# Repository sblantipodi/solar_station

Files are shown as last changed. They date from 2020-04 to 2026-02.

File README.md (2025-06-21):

# Solar Station
Smart solar watering system  
_Written for Arduino IDE and PlatformIO._







If you like **Solar Station**, give it a star, or fork it and contribute!




Project is bootstrapped with my [Arduino Bootstrapper](https://github.com/sblantipodi/arduino_bootstrapper) library and my [PlatformIO version increment](https://github.com/sblantipodi/platformio_version_increment) script.

## Credits
- Davide Perini

## Components:
  - Arduino C++ sketch running on an ESP8266EX D1 Mini from Lolin running at 80MHz or ESP32-S3
  - Raspberry + Home Assistant for Web GUI, automations and MQTT server
  - 88x142 5V solar panel
  - Sony VCT6 18650 Lithium Battery
  - TP4056 protected lithium charger
  - MT3608 DC DC step up module to step up battery voltage @ 5.5V, ESP chip is happy with it
  - MT3608 DC DC step up module to step up battery voltage @ 8.66V, water pump is powerful with it
  - Relay Shield to safely power the water pump and "detach it from the circuit"
  - (100kΩ + (22kΩ + 4.7kΩ)) voltage divider for Battery voltage level monitoring circuit (see Voltage divider section for ESP32-S3)
  - 3.5V/9V water pump (3W @ 9V)
  - TTP223 capacitive touch button with A contact soldered (HIGH signal when button is not pressed, 
    LOW signal when button is pressed), used to reset the microcontroller
  - Google Home Mini for Voice Recognition
  
## Schematic  
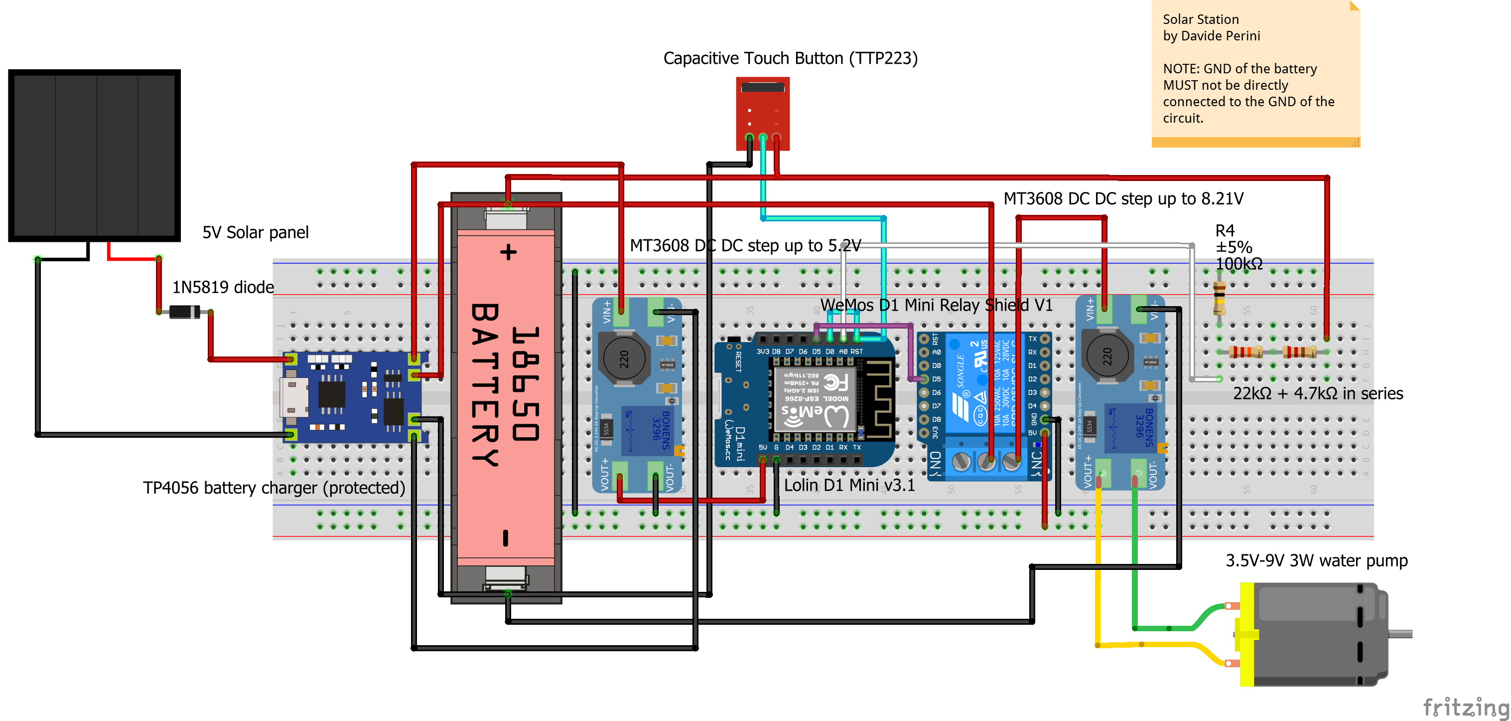
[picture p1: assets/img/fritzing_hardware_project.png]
CIRCUITS


## First working project


## Final working project with two DC to DC step up modules
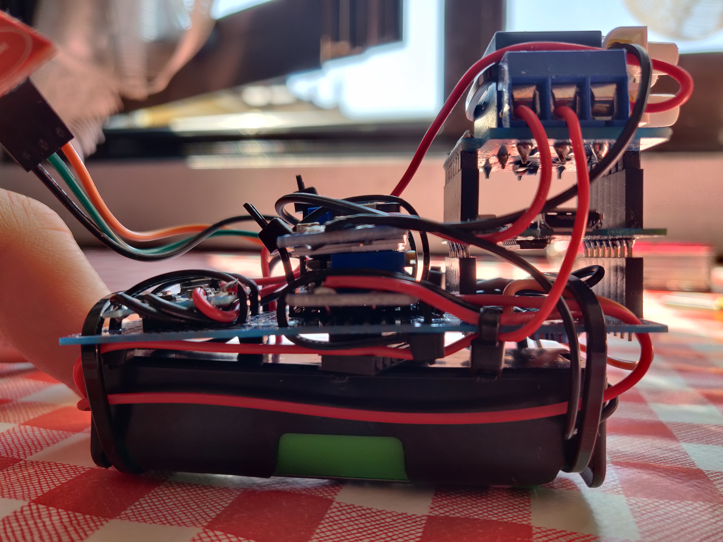
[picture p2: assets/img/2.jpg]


## Voltage divider:

- Voltage source = 4.2V (lithium battery at max)
- R1 = 100kΩ 
- R2 = 22kΩ + 4.7kΩ (in series)
- Voltage Out = 3.3V (maximum voltage that a D1 Mini can read from the analog pin)

EDIT: Project has been updated to work with an ESP32-S3. ESP32-S3 ADC pin reads up to 3.1V (with an attenuation of 11DB),
for this reason I swapped the R2 resistors with a 22kΩ + 10kΩ + 4.7kΩ (in series).

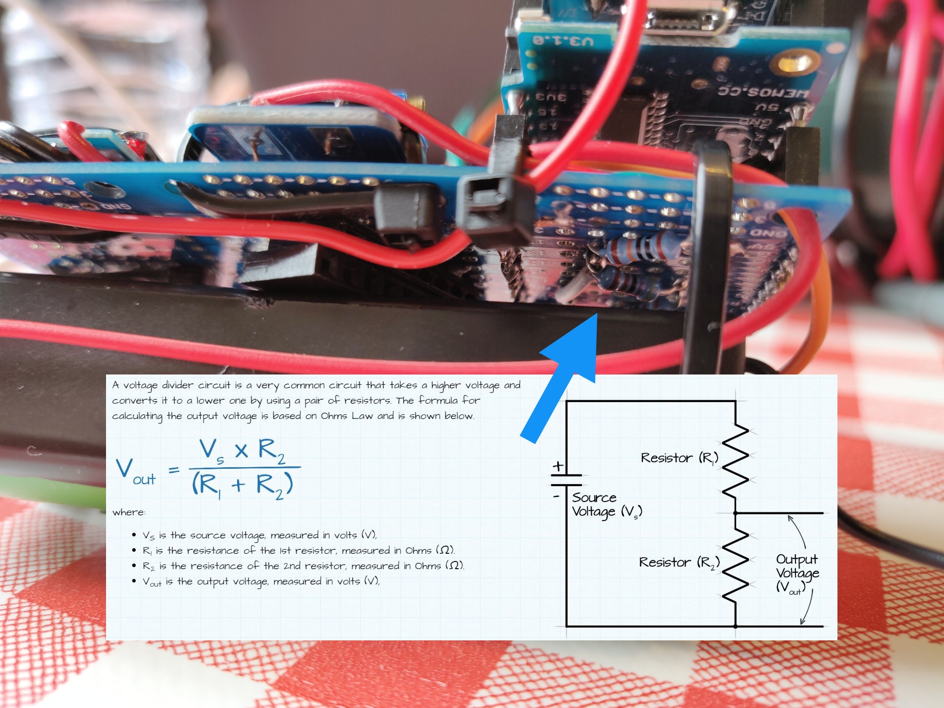
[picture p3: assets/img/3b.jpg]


## From the top
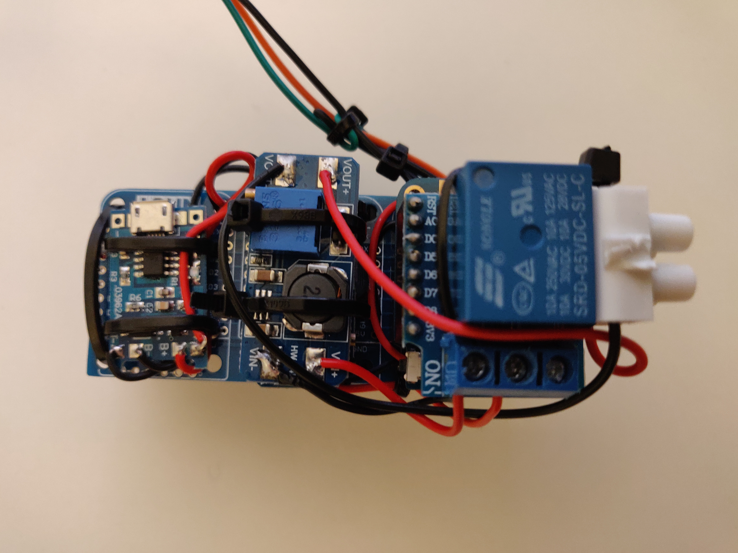
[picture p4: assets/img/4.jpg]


## Water pump
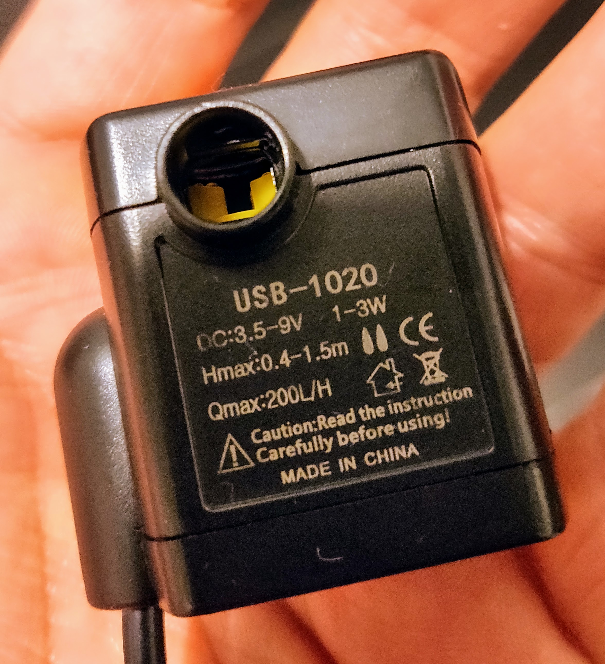
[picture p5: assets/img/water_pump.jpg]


## IP56 box


## Second iteration of the same project for other plants in a non stacked format
  

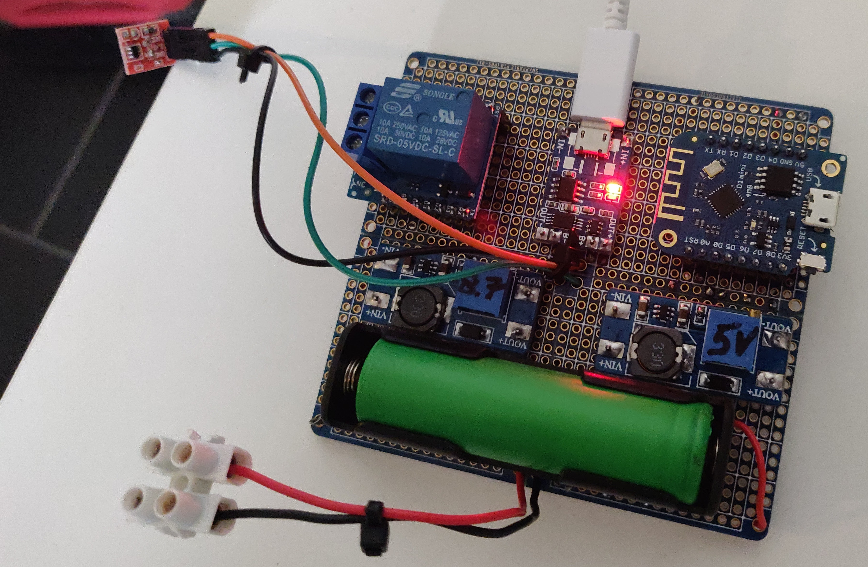
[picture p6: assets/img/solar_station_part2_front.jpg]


## Home Assistant Mobile Client Screenshots
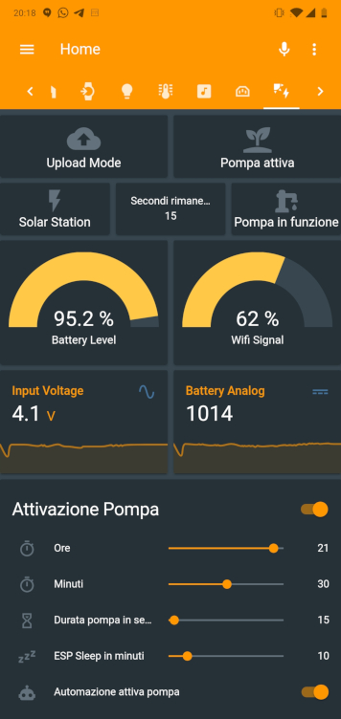
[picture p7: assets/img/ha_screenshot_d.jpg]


## License
This program is licensed under MIT License

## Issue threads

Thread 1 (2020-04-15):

Questions

bobkelso974, 2020-04-15:
Hello
I'm interested in your project
I'd like to ask you a few questions:
What model of water pump do you use?
How long do you run this pump? (deep sleep time?)
Is it for indoor or outdoor use?
And finally, does it work well?

I made about the same circuit.
Except I didn't put a relay but a Mosfet for energy saving.

Thank you

sblantipodi, 2020-04-26:
@bobkelso974 sorry for the late reply.
I'm using a 3.5V-9V 1-3W water pump.

I have added an image of the pump in the readme of the project.
https://github.com/sblantipodi/solar_station

You can find similar pump on amazon, it works very very well.
I run it at 8.6V so a little bit less than 3W and it is very powerful and quiet.

Pump runs for 30 seconds a day because I use it for a small watering system.
Take a look at the readme, there is an IP56 box for outdoor use.
The ESP sleeps for 10 minutes and it stays on the time needed to read the configuration from the MQTT server and send back its state.
Basically when the ESP wake up reads the configuration from the MQTT server, this config says to the ESP if the pump must be on and the number of seconds that it must be turned on.

I can say that the system works very very well.

bobkelso974, 2020-04-27:
Thank you for your answers.
I have the same model of water pump as you but I have a problem, I have almost the same circuit as you expected the relay is replaced by a mosfet
The problem is on my mt3608. When I set the voltage to 8v, I have a hiss on this module and when the pump is running the voltage goes up to 10v ...
When I test with a mini USB boost converter 3V-5V, it works well. I tested several MT3608 same problem
Did you have the same type of problem? Or do you have an idea where it can come from?

sblantipodi, 2020-04-27:
mmm...
A hiss is not necessary a problem, it could be the normal "coil whine" but it's not normal that if you set the MT3608 to output 8V it output 10V.

Is your MT3608 connected to the battery directly like in my circuit?
If your battery able to handle the load of the pump?
Battery tends to have a big voltage drop when something like a motor is connected, after the motor startup the voltage returns to normal and this may cause some spikes.
A good capacitor can help with this problem or probably try to choose a better 18650 battery rated for high drain. I know that 3W is not that much for a 18650 (I hope you are using a 18650) but motors are a bit tricky because they cause huge voltage drops and spikes on power supply.

sblantipodi, 2020-04-27:
@bobkelso974 another reason why I choosed the relay is because relays provide isolation between the command circuit, this isolation is a good thing when using motors.

Mosfets have a "body diode" and the body is normally connected to the source and this is not desirable when using motors or things that can provide some big inrush current in your circuit

bobkelso974, 2020-04-28:
thank you for all your answers
I'm going to do some tests, including a relay to replace the mosfet...

Closed 2020-06-08.

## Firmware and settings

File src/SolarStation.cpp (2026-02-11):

/*
  SolarStation.cpp - Smart solar watering system 
  
 Copyright © 2020 - 2026  Davide Perini
  
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
  * Components:
   - Arduino C++ sketch running on an ESP8266EX D1 Mini from Lolin running at 80MHz
   - Raspberry + Home Assistant for Web GUI, automations and MQTT server
   - 88x142 5V solar panel
   - Sony VCT6 18650 Lithium Battery
   - TP4056 protected lithium charger
   - MT3608 DC DC step up module to step up battery voltage to 5.5V, ESP chip is happy with it
   - MT3608 DC DC step up module to step up battery voltage to 8.66V, water pump is powerful with it
   - Relay Shield to safely power the water pump and "detach it from the circuit"
   - 100kΩ + 22kΩ + 4.4kΩ resistance for Battery voltage level monitoring circuit
   - 3.5/9V water pump (3W @ 9V)
   - TTP223 capacitive touch button with A contact soldered (HIGH signal when button is not pressed, 
     LOW signal when button is pressed), used to reset the microcontroller
   - Google Home Mini for Voice Recognition
   NOTE: GND of the battery MUST not be directly connected to the GND of the circuit.
*/

#include <SolarStation.h>


/********************************** START SETUP*****************************************/
void setup() {
#if defined(ARDUINO_ARCH_ESP32)
  rgbLedWrite(LED_BUILTIN, 0, 0, 0);
#endif
  // if fastDisconnectionManagement we need to execute the callback immediately,
  // example: power off a watering system can't wait MAX_RECONNECT attemps
  fastDisconnectionManagement = true;
#if CONFIG_IDF_TARGET_ESP32C3 || CONFIG_IDF_TARGET_ESP32S2 || CONFIG_IDF_TARGET_ESP32S3
  Serial.setTxTimeoutMs(0);
#endif
  Serial.begin(SERIAL_RATE);

  pinMode(WATER_PUMP_PIN, OUTPUT); // setup water pump pin
  digitalWrite(WATER_PUMP_PIN, LOW); // turn off the pump just in case

#if defined(ESP8266)
  pinMode(OLED_RESET, OUTPUT);  // setup built in ESP led
  digitalWrite(OLED_RESET, HIGH); // turn off the ESP led
#else
  pinMode(ANALOG_IN_PIN, INPUT); //It is necessary to declare the input pin
#endif
#if defined(ARDUINO_ARCH_ESP32)
  rgbLedWrite(LED_BUILTIN, 0, 0, 0);
#endif
  // Bootsrap setup() with Wifi and MQTT functions
  blockingMqtt = false;
  bootstrapManager.bootstrapSetup(manageDisconnections, manageHardwareButton, callback);

#if CONFIG_IDF_TARGET_ESP32C3 || CONFIG_IDF_TARGET_ESP32S2 || CONFIG_IDF_TARGET_ESP32S3
  // Use 12 bit width (analog reading up to 4095), with DB_11 attenuation (up to 3.1V) on ADC1_CHANNEL_1 (GPIO 2)
  // https://docs.espressif.com/projects/esp-idf/en/v4.4/esp32s3/api-reference/peripherals/adc.html
  // NOTE those lines where commented in the migration from Arduino Core 2 to Core 3
  // adc1_config_width(ADC_WIDTH_BIT_12);
  // adc1_config_channel_atten(ADC1_CHANNEL_1, ADC_ATTEN_DB_12);
#endif
  readAnalogBatteryLevel();
#if defined(ARDUINO_ARCH_ESP32)
  rgbLedWrite(LED_BUILTIN, 0, 0, 0);
#endif
}

/********************************** MANAGE WIFI AND MQTT DISCONNECTION *****************************************/
void manageDisconnections() {

  // Shut down water pump on small disconnections
  if (wifiReconnectAttemp > 10 || mqttReconnectAttemp > 10) {
      digitalWrite(WATER_PUMP_PIN, LOW);      
  }
  // Shut down ESP on MAX_RECONNECT attemp
  if (wifiReconnectAttemp > MAX_RECONNECT || mqttReconnectAttemp > MAX_RECONNECT) {
      espDeepSleep(false, true);
  }

}

/********************************** MQTT SUBSCRIPTIONS *****************************************/
void manageQueueSubscription() {

  bootstrapManager.subscribe(SOLAR_STATION_UPLOADMODE_TOPIC);      
  bootstrapManager.subscribe(SOLAR_STATION_WATERPUMP_ACTIVE_TOPIC);      
  bootstrapManager.subscribe(SOLAR_STATION_MQTT_CONFIG, 1);      
  bootstrapManager.subscribe(SOLAR_STATION_MQTT_ACK);
      
}

/********************************** MANAGE HARDWARE BUTTON *****************************************/
void manageHardwareButton() {

  // no need to manage hardware button, TP223 is used to reboot the ESP and does not need code to do it

}

/********************************** START CALLBACK *****************************************/
void callback(char* topic, byte* payload, unsigned int length) {

  JsonDocument json = bootstrapManager.parseQueueMsg(topic, payload, length);

  if(strcmp(topic, SOLAR_STATION_MQTT_CONFIG) == 0) {
    processMQTTConfig(json);
  } else if(strcmp(topic, SOLAR_STATION_MQTT_ACK) == 0) {
    processAckTopic(json);
  } else if(strcmp(topic, SOLAR_STATION_UPLOADMODE_TOPIC) == 0) {
    processUploadModeJson(json);
  } 

}

/********************************** START PROCESS JSON *****************************************/
bool processMQTTConfig(JsonDocument json) {

  timedate = helper.getValue(json["time"]);

  String uploadModeStr = json["upload_mode"];
  uploadMode = uploadModeStr == on_CMD;
  if (uploadMode) {
    nowMillisSendStatus = millis(); // reset the counter, first ten seconds the blu led will be on
  }

  String waterPumpActiveStr = json["pump_active"];
  waterPumpActive = waterPumpActiveStr == on_CMD;

  // reconnection can cause mqttConfig to be reprocessed. don't reinitialize number of attemps
  if (!dataMQTTReceived) {
    if (waterPumpActive) {
      number_of_attemps = number_of_attemps - 6;
    } else {
      number_of_attemps = number_of_attemps - 4;
    }
  }
  
  String pumpSecondsStr = json["pump_seconds"];
  waterPumpSecondsOn = pumpSecondsStr.toDouble() * 1000;

  String espSleepTimeMinutesStr = json["esp_sleep_time_minutes"];
  
  // if sleepTime is 1 sleep 1 second, if it's 61 sleep forever, sleep N minutes otherwise
  if ((espSleepTimeMinutesStr.toDouble() >= 1)) {
    espSleepTime = (espSleepTimeMinutesStr.toDouble() * 60 * 1000000);
  } else {
    espSleepTime = (1e6);
  }
  if ((espSleepTimeMinutesStr.toDouble() >= 61)) {
    espSleepTime = 0; // 0 means sleep forever
  }

  // dataMQTTReceived enables sketch processing, we do our things only after MQTT config has been received
  dataMQTTReceived = true;

  // Reset the millis used for water pump activity
  nowMillisWaterPumpStatus = millis();
  // Reset the millis used for send status activity
  nowMillisSendStatus = millis();
  // Reset the millis used for force deep sleep after 15 minutes
  nowMillisForceDeepSleepStatus = millis();
  // Reset the millis used for MQTT QoS1
  onStateNowMillis = millis();
  offStateNowMillis = millis();
  waterPumpPowerStateOnNowMillis = millis();
  waterPumpPowerStateOffNowMillis = millis();
  sensorStateNowMillis = millis();
  waterPumpActiveStateOffNowMillis = millis();

  // if battery analog level is below 3700 (3.7V) the microcontroller can continue to wake up and sleep but it can't turn on the water pump
  int batteryVoltage = readAnalogBatteryLevel();
  waterPumpCutOff = (batteryVoltage < WATER_PUMP_CUTOFF);
  // if battery analog level is below 3500 (3.5V) hard cut off
  espCutOff = (batteryVoltage < ESP_CUTOFF);
  return true;

}

// ACK Automation for custom implementation of QoS1 in pubsubclient that doesn't support QoS1 for publish if not for subscribe
bool processAckTopic(JsonDocument json) {

    String ackMsg = json[VALUE];

    if (ackMsg == "sendOnState") {
      onStateAckReceived = true;
    } else if (ackMsg == "sendOffState") {
      offStateAckReceived = true;
    } else if (ackMsg == "sendWaterPumpPowerStateOff") {
      waterPumpPowerStateOffAckReceived = true;
    } else if (ackMsg == "sendWaterPumpPowerStateOn") {
      waterPumpPowerStateOnAckReceived = true;
      waterPumpPower = true;
      // This runs until the pump is off if the batt voltage is greater than 3.6V
      digitalWrite(WATER_PUMP_PIN, HIGH); // PHISICALLY TURN ON THE PUMP!!!
      // Turning on water pump, resetting the millis counter used to turn it off
      nowMillisWaterPumpStatus = millis();
    } else if (ackMsg == "sendSensorState") {
      sensorStateAckReceived = true;
    } else if (ackMsg == "sendWaterPumpActiveStateOff") {
      waterPumpActiveStateOffAckReceived = true;
    }
    
    return true;

}

bool processUploadModeJson(JsonDocument json) {

    uploadMode = (helper.isOnOff(json) == ON_CMD);
    Serial.println();
    Serial.print("UPLOAD_MODE= "); Serial.println(uploadMode);    
    Serial.println();
    return true;

}

/********************************** SEND STATE *****************************************/
void sendSensorState() {

  if(millis() > sensorStateNowMillis + DELAY_1000){
    sensorStateNowMillis = millis();
    number_of_attemps++;
    sendSensorStateNotTimed();
  }

}
void sendSensorStateNotTimed() {  

  JsonObject root = bootstrapManager.getJsonObject();

  // read analog battery level 
  int batteryLevelAnalog = readAnalogBatteryLevel();

  // if the analog value is below 3500 (3.5V) execute an hard cutoff
  if (espCutOff) {
    hardCutOff = true;
    root["HARD_CUT_OFF"] = true;
  } else {
    root["HARD_CUT_OFF"] = false;
  }
  if (waterPumpCutOff) {
    root["WATER_PUMP_CUT_OFF"] = true;
  } else {
    root["WATER_PUMP_CUT_OFF"] = false;
  }
  if (batteryLevelOnboot == -1) {
    root["battery_level_on_boot"] = batteryLevelAnalog;
    batteryLevelOnboot = batteryLevelAnalog;
  }
  root["battery"] = batteryLevelAnalog;
  root["frequency"] = ESP.getCpuFreqMHz();  
  
  bootstrapManager.sendState(SOLAR_STATION_STATE_TOPIC, root, VERSION); 

  delay(DELAY_10);

  // hardCutOff but only if uploadMode is false
  if (hardCutOff && !uploadMode) {
    espDeepSleep(true, true);
  }

}

void sendSensorStateAfterSeconds(int delay) {

  if(millis() > nowMillisSendStatus + delay){
    nowMillisSendStatus = millis();
    sendSensorStateNotTimed();
  }

}

void sendOnState() {    

  if(millis() > onStateNowMillis + DELAY_1000){
    sendOnOffState(ON_CMD, onStateNowMillis);     
  }

}

void sendOffState() {

  if(millis() > offStateNowMillis + DELAY_1000){
    sendOnOffState(OFF_CMD, offStateNowMillis);
  }
  
}

void sendOnOffState(String cmd, unsigned long stateMillis) {
  
  number_of_attemps++;
  Serial.println("SENDING STATE"); Serial.println(cmd);

  JsonObject root = bootstrapManager.getJsonObject();

  root["state"] = cmd;
  if (cmd == OFF_CMD) {
    offStateNowMillis = millis();
    root["number_of_attemps"] = number_of_attemps;
  } else {
    onStateNowMillis = millis();
    root["number_of_attemps"] = 0;
  }

  bootstrapManager.publish(SOLAR_STATION_POWER_TOPIC, root, false);

  delay(DELAY_10);

}

void sendWaterPumpPowerStateOff() {

  if(millis() > waterPumpPowerStateOffNowMillis + DELAY_1000){
    waterPumpPowerStateOffNowMillis = millis();
    number_of_attemps++;
    Serial.println(); 
    Serial.print("SENDING WATER PUMP POWER STATE OFF");
    bootstrapManager.publish(SOLAR_STATION_WATERPUMP_POWER_TOPIC, helper.string2char(OFF_CMD), false);
    delay(DELAY_10);
  }

}

void sendWaterPumpPowerStateOn() {

  if(millis() > waterPumpPowerStateOnNowMillis + DELAY_1000){
    waterPumpPowerStateOnNowMillis = millis();
    number_of_attemps++;
    Serial.println(); 
    Serial.print("SENDING WATER PUMP POWER STATE ON"); 
    bootstrapManager.publish(SOLAR_STATION_WATERPUMP_POWER_TOPIC, helper.string2char(ON_CMD), false);
    delay(DELAY_10);
  }

}

void sendWaterPumpActiveStateOff() {

  if(millis() > waterPumpActiveStateOffNowMillis + DELAY_1000){
    waterPumpActiveStateOffNowMillis = millis();
    number_of_attemps++;
    Serial.println(); 
    Serial.println("SENDING WATER PUMP ACTIVE STATE OFF"); 
    bootstrapManager.publish(SOLAR_STATION_WATERPUMP_ACTIVE_STAT_TOPIC, helper.string2char(OFF_CMD), false);
    delay(DELAY_10);
  }

}

/********************************** WATER PUMP MANAGEMENT (non blocking delay) *****************************************/
void turnOffWaterPumpAfterSeconds() {

  if(millis() > nowMillisWaterPumpStatus + waterPumpSecondsOn){
    nowMillisWaterPumpStatus = millis();
    waterPumpPower = false;
    digitalWrite(WATER_PUMP_PIN, LOW); // PHISICALLY TURN OFF THE WATER PUMP
  }

}

/********************************** ESP DEEP SLEEP *****************************************/
// Note: to achieve timed deepSleep you need to connect D0 with RST pin
void espDeepSleep(bool sendState, bool hardCutOff) {

  // if sendState is required, shutdown the microcontroller after the offStateAckReceived only
  if (sendState && !offStateAckReceived) {
    sendOffState();
  }
  if (sendState && offStateAckReceived) {
    espDeepSleep(hardCutOff); 
  }
  // if sendState is not required, MQTT or Wifi not available for example, shutdown microcontroller
  if (!sendState) {
    espDeepSleep(hardCutOff);
  }

}
void espDeepSleep(bool hardCutOff) {
  dataMQTTReceived = false;
  delay(DELAY_1000);
#if CONFIG_IDF_TARGET_ESP32S3
#endif
  // if hardCutOff sleep forever or until capacitive button is pressed
    if (hardCutOff || espSleepTime == 0) {
#if defined(ESP8266)
    ESP.deepSleep(0);
#else
      esp_deep_sleep_start();
#endif
  } else {
    ESP.deepSleep(espSleepTime);
  }

}
// force deepSleep after 15 minutes
void forceDeepSleep() {

  if(millis() > nowMillisForceDeepSleepStatus + FORCE_DEEP_SLEEP_TIME){
    nowMillisForceDeepSleepStatus = millis();
    digitalWrite(WATER_PUMP_PIN, LOW);
    espDeepSleep(false, true);
  }

}

/********************************** BATTERY LEVEL *****************************************/
// read analog battery level from A0 pin (voltage divider required on that PIN because ESP can read up to 3.3V and the battery goes up to 4.2V)
int readAnalogBatteryLevel() {

  return analogRead(ANALOG_IN_PIN);

}

/********************************** START MAIN LOOP *****************************************/
void loop() {  
  
  // Bootsrap loop() with Wifi, MQTT and OTA functions
  bootstrapManager.bootstrapLoop(manageDisconnections, manageQueueSubscription, manageHardwareButton);

  // Send status on startup and wait for MQTT config, this is subscribed with QoS1 so MQTT server will retry until received
  if (!onStateAckReceived || !dataMQTTReceived) {
    sendOnState();
  }
 
  // MQTT config received, job start (MQTT Config sent via HA in QoS1)
  if (dataMQTTReceived && onStateAckReceived) {
    if (uploadMode) {
      digitalWrite(WATER_PUMP_PIN, LOW);
      sendSensorStateAfterSeconds(TENSECONDSPERIOD); // this sendState does not wait for an ack    
    } else {
      // if battery analog level is below 816 (3.3V) the microcontroller can continue to wake up and sleep but it can't turn on the water pump
      if (waterPumpActive && !waterPumpCutOff) {      
        // Water pump active, if the pump was off, send sensor state and pump state for the first time              
        if (!sensorStateAckReceived) {
          sendSensorState();
        } else {
          if (!waterPumpPowerStateOnAckReceived) {            
            sendWaterPumpPowerStateOn();                                             
          } else {
            if (waterPumpPower) {
              turnOffWaterPumpAfterSeconds(); // Pump is turned off as soon as the delay is reached, no matter for ACK from the MQTT server
              // continue to send state every seconds when the pump is turned on
              sendSensorStateAfterSeconds(DELAY_1000); // this sendState does not wait for an ack    
            } else {
              if (!waterPumpPowerStateOffAckReceived) {
                sendWaterPumpPowerStateOff(); // Update the MQTT server with off state of the pump when it is possible
              } else {
                if (!waterPumpActiveStateOffAckReceived) {
                  sendWaterPumpActiveStateOff();
                } else {
                  espDeepSleep(true, false);
                  // Pump is turned off, microcontroller is finally sleeping
                }
              }                            
            }          
          }                          
        }         
      } else {
        // Water pump was not active, send state and sleep until next
        digitalWrite(WATER_PUMP_PIN, LOW);
        if (!waterPumpPowerStateOffAckReceived) {
          sendWaterPumpPowerStateOff();
        } else {
          if (!sensorStateAckReceived) {
            sendSensorState();
          } else {
            espDeepSleep(true, false);
          }          
        }        
      }
    }
  }

  // Force deepSleep after 15 minutes of activity, no matter what's happening, some errors occured probably.
  forceDeepSleep();

  delay(DELAY_10);
  
}

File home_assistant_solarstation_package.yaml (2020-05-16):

switch:
  - platform: mqtt
    name: upload_mode
    command_topic: "cmnd/upload_mode/SLEEP"
    qos: 0
    retain: true
    payload_on: "ON"
    payload_off: "OFF"    
    optimistic: false
  - platform: mqtt
    name: water_pump_active
    command_topic: "cmnd/water_pump/ACTIVE"
    state_topic: "stat/water_pump/ACTIVE"
    qos: 0
    payload_on: "ON"
    payload_off: "OFF"    
    optimistic: false
    retain: false
  - platform: mqtt
    name: water_pump_power
    command_topic: "cmnd/water_pump/POWER"
    state_topic: "stat/water_pump/POWER"
    qos: 1
    retain: false
    payload_on: "ON"
    payload_off: "OFF"         
  - platform: mqtt
    name: "Solar Station"
    command_topic: "cmnd/solarstation/POWER"
    state_topic: "stat/solarstation/POWER"
    qos: 1
    retain: false
    value_template: "{{ value_json['state'] }}"
    state_on: "ON"
    state_off: "OFF"  
    
    
input_number:
    solarstation_activation_hour:
        name: Ore
        icon: mdi:timer
        initial: 21
        min: 0
        max: 23
        step: 1
    solarstation_activation_minute:
        name: Minuti
        icon: mdi:timer
        initial: 30
        min: 0
        max: 59
        step: 1
    waterpump_activation_seconds:
        name: Durata pompa in secondi
        icon: mdi:timer
        initial: 15
        min: 0
        max: 300
        step: 1   
    esp_sleep_time_minutes:
        name: ESP Sleep in minuti
        icon: mdi:timer
        initial: 10
        min: 0
        max: 61
        step: 1           

sensor:
  - platform: mqtt
    state_topic: 'stat/solarstation/POWER'
    name: 'Solar Station mqtt attemps'
    unit_of_measurement: ' '
    value_template: '{{ value_json.number_of_attemps }}'
  - platform: mqtt
    state_topic: 'tele/solarstation/STATE'
    name: 'Last Seen Solar Station'
    value_template: '{{ value_json.time }}'
  - platform: mqtt
    state_topic: 'tele/solarstation/STATE'
    name: 'Battery Analog'
    unit_of_measurement: ' '
    value_template: '{{ value_json.battery }}'  
  - platform: mqtt
    state_topic: 'tele/solarstation/STATE'
    name: 'Wifi Signal'
    unit_of_measurement: ' '
    value_template: '{{ value_json.wifi }}'    
  - platform: mqtt
    state_topic: 'tele/solarstation/STATE'
    name: 'Solar Station Version'
    unit_of_measurement: ' '
    value_template: '{{ value_json.ver }}'  
  - platform: mqtt
    state_topic: 'tele/solarstation/STATE'
    name: 'Solar Station Remaining Seconds'
    unit_of_measurement: ' '
    value_template: '{{ value_json.remaining_seconds }}'      
  - platform: template
    sensors:
      solar_station_battery_percentage_zero_volt:
        friendly_name: 'Battery Level zero volt'
        unit_of_measurement: '%'
        value_template: >-
          {%- if (states("sensor.battery_analog") | int) > 1 %}
            {{ ((states("sensor.battery_analog") | int * 100) / 1024) | round(1) }}
          {%- else -%}
            unknown
          {%- endif -%}
  - platform: template
    sensors:
      solar_station_battery_percentage:
        friendly_name: 'Battery Level'
        unit_of_measurement: '%'
        value_template: >-
          {{ ((100 * (states("sensor.battery_analog") | int - 816)) / (1024-816)) | round(1) }}
  - platform: template
    sensors:
      solar_station_battery_voltage:
        friendly_name: 'Battery Voltage'
        unit_of_measurement: 'V'
        value_template: >-
          {%- if (states("sensor.battery_analog") | int) > 1 %}
            {{ ( ((states("sensor.battery_analog") | int) * 4.14) / 1024) | round(2) }}      
          {%- else -%}
            unknown
          {%- endif -%}
  - platform: template
    sensors:
      activate_water_pump_active:
        friendly_name: 'activate_water_pump_active'
        value_template: >-
          {{ "%0.02d:%0.02d" | format(states("input_number.solarstation_activation_hour") | int, states("input_number.solarstation_activation_minute") | int) }}
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

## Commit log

2020-04-03 first refactor
    [Solar_Station.fzz]
2020-04-06 final hardware fritzing project
    [Solar_Station.fzz]
2020-04-11 circuit optimized, battery gnd disconnected from the circuit for safer operations
    [Solar_Station.fzz]
2020-04-11 battery gnd disconnected from the circuit for safer operations, circuit optimizations
2020-04-11 battery gnd disconnected from the circuit for safer operations, circuit optimized
2020-04-13 Arduino Json update
2020-04-13 battery gnd disconnected from the circuit for safer operations. circuit optimized.
2020-04-20 arduino bootstrapper
2020-04-21 arduino bootstrapper integration
2020-04-23 arduino bootstrap queue manager
2020-04-23 arduino bootstrapper queue manager
2020-04-30 update libs, removed unusful mqtt subscription, upload mode fix
    [SolarStation.cpp, SolarStation.h]
2020-05-08 Arduino Bootstrapper update (v.1.3.0)
2020-05-10 espressif8266 v2.5.1 arduino core v2.7.1
2020-05-16 Arduino Bootstrapper update (v.1.4.5)
2020-06-07 remaining seconds display fix
    [SolarStation.cpp, SolarStation.h]
2020-06-19 Arduino Bootstrapper update (v.1.5.0)
2020-07-17 Updated Arduino core to 2.7.2
2020-07-28 Switch to JetBrains CLion
2020-08-11 Arduino Bootstrapper update (v.1.6.0)
2020-08-20 Arduino Bootstrapper update (v.1.7.0)
2020-09-13 second hardware iteration
    [Solar_Station.fzz]
2020-09-14 hardware project part 2
    [Solar_Station.fzz]
2020-12-19 Arduino Bootstrapper update (v.1.7.3)
2020-12-24 Arduino Bootstrapper update (v.1.7.4)
2020-12-24 Arduino Bootstrapper (v1.7.5)
2021-01-11 Arduino Bootstrapper (v1.7.6)
2021-04-08 Reduced memory footprint
2021-04-08 Arduino Bootstrapper (v1.7.8)
2021-04-18 Arduino Bootstrapper (v1.7.9)
2021-06-07 Arduino Bootstrapper (v1.8.0)
2021-08-13 Arduino Bootstrapper (v1.9.0)
2021-08-18 Arduino Bootstrapper (v1.9.2)
2021-09-16 Arduino Bootstrapper (v1.10.3)
2021-10-16 Arduino Bootstrapper (v1.11.2)
2021-11-13 Arduino Bootstrapper (v1.11.4)
2022-01-27 Arduino Bootstrapper (v1.12.5)
2022-02-28 Arduino Bootstrapper (v1.12.6)
2022-03-11 Arduino Bootstrapper (v1.12.7)
2022-03-18 Arduino Bootstrapper (v1.12.8)
2022-04-29 Arduino Bootstrapper (v1.12.11)
2022-06-06 Arduino Bootstrapper (v1.12.12)
2022-07-22 battery info updated
2022-08-28 Arduino Bootstrapper (v1.13.0)
2022-12-29 Arduino Bootstrapper (v1.13.1)
2022-12-29 Arduino Bootstrapper (v1.13.3)
2022-12-29 Arduino Bootstrapper (v1.13.4)
2023-01-07 esp8266/Arduino 3.1
2023-01-22 Arduino Bootstrapper (v1.13.5)
2023-03-13 Arduino Bootstrapper update (v.1.14.0)
2023-06-19 Arduino Bootstrapper update (v.1.15.1)
2023-06-19 Switch to ESP32-S3
2023-11-26 Arduino Bootstrapper update (v.1.15.3)
2024-01-05 Arduino Bootstrapper update (v.1.16.1)
2024-06-03 Arduino Bootstrapper update (v.1.17.0)
2024-07-05 Arduino Bootstrapper update (v.1.18.0)
2024-08-01 Arduino Bootstrapper update (v.1.18.1)
2024-09-19 Arduino Bootstrapper update (v.1.18.2)
2025-01-26 Arduino Bootstrapper update (v.1.18.3)
2025-04-10 arduino json 7.4
2025-04-11 arduino json 7.4.1
2025-08-17 Arduino Bootstrapper (v1.18.6)
2026-05-02 arduino_bootstrapper platformio_version_increment update

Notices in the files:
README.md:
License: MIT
